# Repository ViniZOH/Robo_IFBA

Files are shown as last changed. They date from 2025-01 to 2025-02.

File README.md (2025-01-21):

# Principais Modificações

## 21/01/2025 -- Aplicadas no ultimo codigo

-------------------------------------------------------
Principais Problemas
-------------------------------------------------------

1- Desativação do motor fora do range de segurança: Quando o input_mot está fora dos limites de segurança, os motores são desligados, mas o setpoint do PID não é atualizado ou monitorado ativamente.
2- Inconsistência na direção do controle: O controle parece atuar apenas em um sentido (subindo até o setpoint), mas não reativa para corrigir valores que excedam o setpoint.
3- Falta de condições dinâmicas no PID: O PID precisa calcular continuamente e ajustar o motor, independentemente do valor atual de input_mot.
-------------------------------------------------------
Sugestões de Correções
-------------------------------------------------------
1. Atualizar o cálculo do PID continuamente:
O PID deve ser acionado mesmo quando input_mot está fora do intervalo de segurança, garantindo que o sistema tente corrigir para o setpoint.
2. Adicionar lógica para ativar o motor corretamente:
A direção do motor deve ser determinada pela diferença entre input_mot (valor lido no  potenciometro) e set_point_mot (valor alvo do PID).
Lógica Sugerida:
1- Se input_mot < set_point_mot, o motor deve girar em uma direção (para aproximar-se do alvo).
2- Se input_mot > set_point_mot, o motor deve girar na direção oposta (para aproximar-se do alvo).
3- Se input_mot estiver próximo o suficiente do set_point_mot (dentro de uma margem de tolerância), o motor deve parar.

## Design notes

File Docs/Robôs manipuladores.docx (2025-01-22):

“SULLA, que sentava inerte durante o ditato, agora digita rapidamento por alguns segundos e para, removendo completamente a carta.” R.O.R., Karel Capek.

Resumo

Este trabalho relata a recuperação de um equipamento que ficou abandonado no instituto federal da bahia por mais de 10 anos, sem nunca ter sido usado. Um braço robótico RD5NT, da Didactica Itália. A estrutura eletrônica não existia e a estrutura mecânica encontra-se com muitos pontos de oxidação. Ao final do trabalho, o robô foi entregue com nova estrutura de controle de potência, posicionamento dos motores, e uma adaptação técnica para o fechamento do efetuador. As estruturas novas foram montadas com componentes adquiridos pelos alunos. Além disso, o robô passou a ter nova estrutura de programação, mais moderna e flexível. Na introdução será mostrado o robô em questão e discutidos os temas introdutórios da robótica de manipulação. Na etapa de Planejamento serão mostrados os componentes escolhidos e os circuitos montados. Na etapa de Execução será mostrada a programação realizada, os circuitos montados e o estado final do braço robótico. Esse trabalho termina com uma lista de próximos passos para continuar melhorando o equipamento.

Abstract

This work reports the recovery of an equipment left in abandonment in Federal Institute of Bahia for more than 10 years, which was never used. A Robotic Arm RD5NT from Didactica Itália. The electronic strutucture does not exist and the mechanical struture is damaged by oxidation. At the end, the arm was returned with new power and positioning structure, and a technical adaptation for the end effector. The new structures were mounted with componentes acquired by the students. Also, the robot has now a new programming structure, modern and more flexibel. Introduction will be shown the robot in question and discussed the introductory topics of robotics manipulation. In the Planning phase will be shown the chosen components and circuits planned. Execution will shown the control programmed, the assembled circuits and the final state of the robotic arm. This work finishes with possible steps to further improve the equipment.

Introdução

Foi numa peça de teatro chamada Rossum’s Universal Robot, de 1921, do checo Karel Capek, que o termo Robot foi introduzido ao mundo. A palavra tem origem em Robota, que significa trabalho forçado. A peça relata um pedaço da vida de Rossum, um cientista de responsável pela criação de um composto químico cuja aplicação seria na construção de humanoides, com o objetivo de transferir todo o trabalho pesado para eles. Hoje, os robôs que conhecemos fazem trabalhos diversos, desde a complexa manipulação de objetos pesados até as mais tediosas e enfadonhas tarefas de casa.

O que se percebe é o aumento do seu uso, já que as pessoas têm menos tempo disponível para as atividades enfadonhas e repetitivas, e não querem correr riscos com atividades como a troca de peças pesadas num forno a 1200ºC, comuns em ambientes industriais, que têm ganhado competitividade com a aplicação desta tecnologia. Aliás, é nesses ambientes que as maiores vantagens destes sistemas aparecem: menores custos de trabalho, maior precisão e maior produtividade, flexibilidade moderada porém alcançável, graças às reprogramações.

Uma definição atual traria o robô como sistema ou grupo de sistemas mecatrônicos capazes de realizar trabalhos de maneira autônoma ou pré-programada. Como elemento principal desta definição temos a programabilidade. O robô como conhecemos advém do pós desenvolvimento da teleoperação (aplicada até em exploração espacial) e do CNC (controle numérico computadorizado), e logo após começaram as aplicações em que não seria possível a utilização de um homem, como a exploração submarina de longa duração, a exploração exoplanetária, o desarmamento de dispositivos explosivos e a busca em ambientes radioativos. Assim, reforça-se que as aplicações dos robôs não estão reduzindo postos de trabalho, pela substituição de um humano com a sua introdução, e sim aumentando a nossa longevidade.

O robô que foi restaurado neste trabalho é um RD5NT, da Didactica Itália. O exemplar da instituição encontrava-se sem estrutura de programação, sem estrutura eletrônica e com marcas de oxidação, apenas com o funcionamento dos servomotores das juntas e do motor do efetuador preservados, o que motivou a restauração.

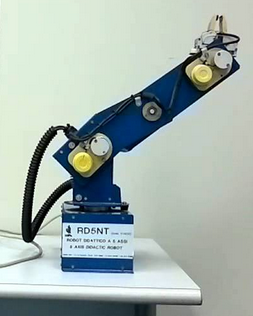
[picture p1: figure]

Trata-se de um braço mecatrônico com 4 servomecanismos de rotação (base, ombro, cotovelo e pulso), 5 elos mecânicos e uma garra mecatrônica. Os elos são as estruturas mecânicas que se ligam entre as juntas, com função de principal de suportar a carga mecânica suportada pelo robô. As juntas que são as estruturas responsáveis pela movimentação e posicionamento e ligam dois elos ou um elo e um efetuador e podem ser do tipo rotacional ou translacional (são os servomecanismos de rotação). Já o efetuador é o dispositivo responsável por realizar a ação proposta, seja ela a soldagem de dois componentes, o suporte de uma peça, a execução de um furo ou o disparo de uma arma. Eles podem ser pneumáticos, mecatrônicos, hidráulicos ou eletromagnéticos.

Além dos componentes citados, um robô precisa para o seu funcionamento de uma unidade de potência para o acionamento correto dos servomecanismos, e uma unidade de controle que proporcionará trajetórias condizentes com a ação a ser efetuada por ele. Para tarefas como complexas como a usinagem de peças para a indústria aeronáutica, por exemplo, o efetuador deve seguir uma trajetória planejada com altíssima precisão. No entanto, para alcançar a melhor estratégia de controle é necessário um modelo matemático do robô. Tal modelagem não foi alcançada, por restrições de tempo do projeto. Além da unidade de controle, é necessária também uma unidade de processamento, responsável por informar a unidade de controle qual posição deve ser alcançada pelo sistema, muitas vezes com restrições de tempo e velocidades bem severas. Esta unidade lê as posições (indicadas provavelmente, por um homem), planeja a movimentação, e se comunica com o espaço exterior, quando necessário.

Para as unidades de controle e processamento, foi adquirido um sistema Arduíno e para as unidades de potência foram adquiridos circuitos do tipo Ponte H (L298N). As características básicas dos componentes adquiridos serão detalhadas na parte de planejamento.

Os robôs manipuladores podem ser classificados por vários critérios, tais como sua geometria, ou estrutura cinemática, o tipo de aplicação para a qual foram projetados, a maneira pela qual são controlados, etc. O robô em questão possui as juntas de rotação numa configuração esférica, seguida por mais dois graus de liberdade de rotação e o efetuador final. A esse tipo é dado o nome RRR (como 3 rotações em sequência). Tem arranjo cinemático antropomórfico do tipo braço.

Planejamento

Levantado o estado atual do robô, no qual verificamos a integridade das conexões entre a porta de saída e os motores, potenciômetros de posição e chave de fim de curso, iniciamos o detalhamento do que seria necessário construir ou comprar para colocar o equipamento em funcionamento. A porta de saída tem vinte e cinco pinos dos quais oito não apresentavam conexão com o robô. As conexões identificadas foram: motor_1, pinos 1 e 14; motor_2, pinos 2 e 15; motor_3, pinos 4 e 17; motor_4, pinos 5 e 18; motor_garra, pinos 6 e 19; Pot_1, pino 20; Pot_2, pino 22; Pot_3, pino 23; Pot_4, pino 24. Os Pinos Vcc e Terra são 13 e 25 respectivamente. O pino 7 está aterrado à carcaça. Os pinos não mencionados estão sem conexão. A figura abaixo mostra a configuração da porta do robô.

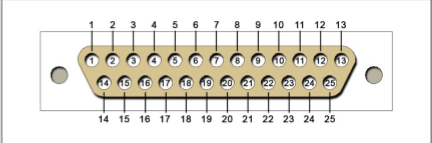
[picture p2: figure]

Como o servomecanismo das juntas é acionadas por motores de corrente contínua, seria necessária a construção de um circuito do tipo Ponte H, para fazê-lo movimentar-se em ambas as direções. Foi adquirida a ponte L298N, uma ponte H completa, com alimentação em 5V e pino de ativação e desativação, capaz de suprir dois motores dc com 2A ou um motor dc com 3A, ou um motor de passo. Na figura abaixo verificamos o desenho esquemático do componente.

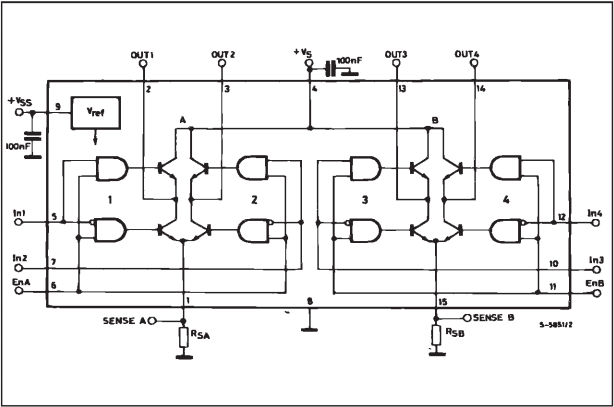
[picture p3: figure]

A ponte integra duas saídas de potência. As duas saídas estão em configuração ponte. Cada ponte é conduzida através de dois gates na entrada e um pino de ativação e desativação. Quando este não tem tensão de alimentação a ponte está no modo desativada. Cada fonte deve ser ligada ao sinal de saída por um caminho bem curto. Para um controle bidirecional de um motor DC é necessário apenas uma das saídas, ou seja, é possível controlar dois motores com um componente. Além disso, foi necessário uma ponte externa de diodos, pois a carga indutiva do motor estava dificultando a própria movimentação.

Para fazer o controle de posição do servomecanismo, foi utilizando um Arduíno MEGA, uma placa de microcontrolador baseado no ATmega1280. Ele tem 54 pinos digitais de entrada/saída (dos quais 14 podem ser usados como saídas PWM), 16 entradas analógicas, 4 UARTs (portas seriais de hardware), um cristal oscilador de 16 MHz, uma conexão USB, um entrada para alimentação e um botão de reset. Ele contém tudo o necessário para apoiar o microcontrolador; basta conectá-lo a um computador com um cabo USB ou ligá-lo com um adaptador AC para DC ou bateria.

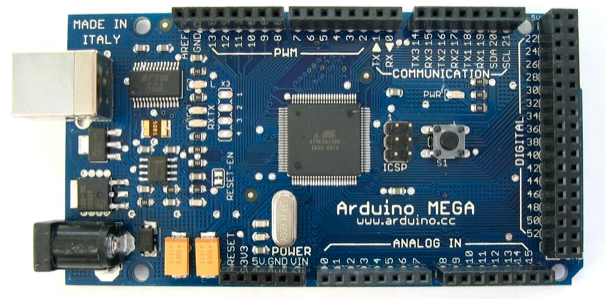
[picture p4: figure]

Com o Arduíno foi possível ler os sinais de tensão dos potenciômetros das juntas, e acionar os circuitos de das entradas das pontes com PWM. Com a saída PWM foi possível controlar com precisão a quantidade de tensão que aciona cada motor e assim realizar o controle de posição e de fechamento da garra.

Além do material descrito, foi utilizada uma fonte de tensão variável para a alimentação dos motores, garra e circuito eletrônico.

Execução

Para a execução do projeto, primeiro foi soldada uma conexão que facilita-se o acesso a porta do robô. Após, realizou-se a verificação das pontes e testou-se o acionamento dos motores direto por elas, verificando a necessidade de 3 pontes para o acionamento de todos os motores do braço antropomórfico.

Foram verificados os limites de movimentação de cada motor e associados a tensão associada fornecida por cada potenciômetro, de modo que para a posição inferior de cada junta haveria um limite de tensão inferior e para cada última posição um limite superior de tensão, sendo possível realizar uma interpolação linear entre os valores. Este mesmo mapeamento foi traduzido numa escala digital para comparação direta com o nível de tensão produzido pelo PWM do Arduíno.

As pontes foram conectadas ao Arduíno, com os pinos de entrada ligados aos pinos de PWM e os pinos de ativação ligados às saídas lógicas do microcontrolador. Após a primeira automação com mudança de direção de movimentação, verificou-se que seria necessária uma ponte de diodos para bloquear a energia acumulada nas bobinas do motor e permitir uma mudança de direção mais rápida. A foto abaixo mostra o estado final do protótipo funcional.

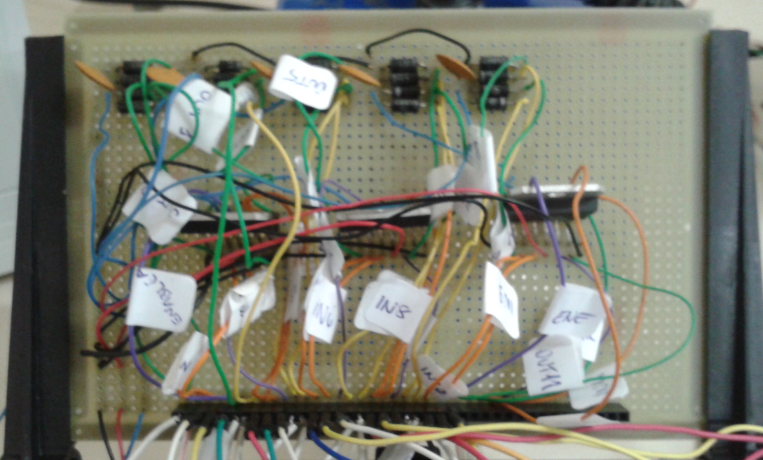
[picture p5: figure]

A partir deste ponto o trabalho tornou-se basicamente de programação. Dentro da unidade Arduíno foi construído um programa que realiza o controle de posição das juntas. Determinamos a posição desejada e aplicamos tensão nos motores até que a posição alcançada esteja de acordo com o solicitado. A posição atual é medida pelo nível de tensão do potenciômetro que é comparada com o nível equivalente à posição de referência. Depois disso o motor é acionado para modificar a sua posição girando para o lado necessário. A posição da junta é novamente calculada e o processo se repete até que a posição solicitada seja alcançada. O diagrama de blocos abaixo retrata o algoritmo utilizado.

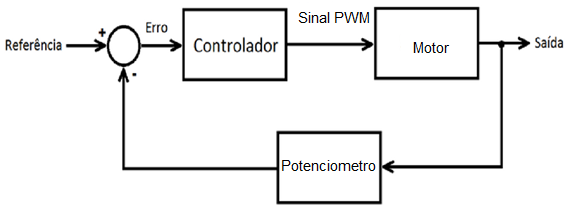
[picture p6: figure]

O algoritmo de controle implementado foi do tipo PID, para o qual apenas a parte proporcional foi utilizada. A estrutura básica de cálculo é reproduzida abaixo. A estrutura na íntegra pode ser visualizada no anexo 1.

error = Setpoint[l] - Input[l];

errSum[l] += (error * timeChange);

dErr = (error - lastErr[l])/timeChange;

Output[l] = (k[l][0])*error + (k[l][1])*errSum[l] + (k[l][2])*dErr;

As etapas do algoritmo descrito acima realizam os seguintes procedimentos:

- calcule a diferença entre posição desejada e posição atual do loop

- calcule o erro acumulado na execução de um loop

- calcule o diferencial do erro em um loop

- calcule e aplique a tensão de saída do loop com base nos parâmetros acima.

Com isso conseguiu-se restaurar a função básica do manipulador, que seria a função de posicionamento. O algoritmo foi implementado para cada uma das juntas rotativas, obtendo sucesso no posicionamento da estrutura em todas elas.

Além do mostrado, foi introduzida uma adaptação técnica à garra, com fins de indicar o fechamento da mesma. A garra só possuía indicador de abertura máxima, realizada por uma chave de fim de curso. A adaptação constiui-se de um circuito de toque, normalmente aberto.

Próximos passos

Há dois pontos cruciais que não foram visitados durante a execução deste projeto. O primeiro é a modelagem da estrutura dinâmica do robô, incluindo as juntas e os elos. Sem essa modelagem não é possível realizar a sintonização da estrutura PID desenvolvida. Sem uma estrutura de PID sintonizada não é possível obter a melhor dinâmica do robô, e deslocamentos em tempos mínimos, além de que, a máxima precisão de posicionamento não é se torna alcançável. É possível o desengripamento das juntas de rotação e substituição das molas de contrabalanceamento.

O segundo ponto crucial é o de determinação da geometria do robô. Sem isso o espaço de trabalho do mesmo é desconhecido, não sendo possível entender em qual zona deste há maior agilidade para a movimentação e reposicionamento de objetos.

Outras ações para o melhoramento futuro da programação são: desenvolvimento da comunicação do Arduíno com o Matlab, aumentando o acesso a ferramentas de identificação e controle para o sistema; Desenvolvimento de uma estrutura de cinemática inversa, para determinação automatizada das posições das juntas para uma dada posição de ação no espaço de trabalho; Desenvolvimento de um código para seguimento de instruções de programação de trajetória em modo manual, a qual tem se tornado de uso constante na indústria automotiva, com as funções de soldagem de ponto elétrico.

Construção de uma base com esteiras e sistema de câmera para a implementação de um simulador de movimentação de carga, permitindo o uso contínuo do robô, em várias disciplinas da instituição.

Pode-se realizar a construção de uma placa apropriada para o sistema de potência do robô, deixando-o independente de fonte externa, com alimentação própria.

Referências

http://www.tech.dmu.ac.uk/~mgongora/Resources/L298N.pdf

http://arduino.cc/en/Main/arduinoBoardMega

ANEXO 1

* Configurando array para medida dos ultimos tempos medidos

*/

unsigned long lastTime[4];

//-------------------------------------------------------------------------------------//

/*

Definindo variavel para controle de inputs e outputs e setpoints

cada linha representa o elo

*/

double Input[4], Output[4], Setpoint[4];

//-------------------------------------------------------------------------------------//

/*

Definido arrays para somatorio dos erros e ultimos erros

*/

double errSum[4]={0,0,0,0},lastErr[4]={0,0,0,0};

//-------------------------------------------------------------------------------------//

/*

configuração do array de ganho dos elos

o numero da linha corresponde o do numero do elo a ser controlado

a coluna corresponde a função de ganho na ordem

1)proporcional

2)integral

3)derivativo

*/

double k[4][3]={{5,0,0},{5,0,0},{5,0,0},{5,0,0}};//arrays com os valores de kp,kd,ki

//----------------------------------------------------------------------------------------//

/*configuração do array de pinos para controle dos elo

linhas representam o elo a ser controlado e colunas as a funcionalidade do tipo

controle do elo 1 (linha 0) o pulso:

pino potenciometro 1 será 1

pino do input 1 do motor 2 será 6

pino do input 2 do motor 2 será 7

pino do enable motor 2 será 33

controle do elo 2 (linha 1)o cotovelo:

pino potenciometro 2 será 2

pino do input 1 do motor 3 será 8

pino do input 2 do motor 3 será 9

pino do enable motor 3 será 35

controle do elo 3 (linha 2)o ombro:

pino potenciometro 3 será 3

pino do input 1 do motor 4 será 10

pino do input 2 do motor 4 será 11

pino do enable motor 4 será 37

controle do elo 4 (linha 3)o ombro:

pino potenciometro 4 será 4

pino do input 1 do motor 5 será 12

pino do input 2 do motor 5 será 13

pino do enable motor 5 será 39

*/

int pino[4][4] = {{1,6,7,33},{2,8,9,35},{3,10,11,37},{4,12,13,39}};

//---------------------------------------------------------------------------------------//

/*configuração de valores medidos

para leitura minima e maxima da entrada analogica

Alimentação do fonte Vs=4.9V

Alimentação da fonte Vss=4.9V

vetor chamado de limites

1)linhas indicam o potenciometro

2)1ª Coluna indica valor maximo de deslocamento angular em relação a referencia

3)2ª Coluna indica valor minimo de setpoint medido pelo arduino

4)3ª COluna indica valor maximo de setpoint medido pelo arduino

*/

double limites[4][3]={{360,0,1023},{293,66,900},{96,376,648},{291,101,928}};

//----------------------------------------------------------------------------------//

unsigned long now;

double timeChange;

double error;

double dErr;

double lasttime;

int condicao;

void setup(){

Serial.end(); //eliminando qualquer configuração serial anterior

//configurando pinos de entrada

for(int i = 0;i<4;i++){

pinMode(pino[i][0],INPUT);

//configurando pinos de saída

for (int j=1;j<4;j++){

pinMode(pino[i][j],OUTPUT);

}

}

pinMode(41,OUTPUT); //Enable do motor 1 - garra

pinMode(43,OUTPUT); //Input 2 do motor 1

pinMode(45,OUTPUT); //Input 1 do motor 1

Serial.begin(57600); //configurando entrada serial

//Verificar estado inicial que se quer da garra

condicaogarra();

//Impondo a codição angular desejada usando a funcao converte angulo detalhes abaixo

for(int i=0;i<4;i++){

Setpoint[i] = converteangulo(i);

}

//iniciando os valores do tempo dos lastTime medidos

for(int j=0;j<4;j++){

lastTime[j]=millis();

}

}

//----------------------------------------------------------------------------------//

void loop()

{

//laço para leitura de todos os potenciometros

Input[0] = analogRead(A1); //potenciometro 1

Input[1] = analogRead(A2); //potenciometro 2

Input[2] = analogRead(A3); //potenciometro 3

Input[3] = analogRead(A4); //potenciometro 4

Serial.println();Serial.println("Diferenca de setpoint");

Serial.print(Setpoint[0]-Input[0]);Serial.print(" | ");

Serial.print(Setpoint[1]-Input[1]);Serial.print(" | ");Serial.print(Setpoint[2]-Input[2]);

Serial.print(" | ");Serial.print(Setpoint[3]-Input[3]);Serial.println(" | ");Serial.println();

//

for(int l=0;l<4;l++){

now = millis();

timeChange = (double)(now - lastTime[l]);

error = Setpoint[l] - Input[l];

errSum[l] += (error * timeChange);

dErr = (error - lastErr[l])/timeChange;

Output[l] = (k[l][0])*error + (k[l][1])*errSum[l] + (k[l][2])*dErr;

//Output[elo] = abs(Output[elo]);

lastErr[l] = error;

lastTime[l] = now;

if(Output[l]>0){

Output[l]=abs(Output[l]);

Output[l]=constrain(Output[l],0,1023);

Output[l]=map(Output[l],0,1023,0,255);

analogWrite(pino[l][1], 0); //acionando input 1 desde que condição de sentido favoravel

analogWrite(pino[l][2], Output[l]); //acionando input 2 desde que condição de sentido favoravel

digitalWrite(pino[l][3],HIGH); //habilitando enable

}

else{

Output[l]=abs(Output[l]);

Output[l]=constrain(Output[l],0,1023);

Output[l]=map(Output[l],0,1023,0,255);

analogWrite(pino[l][1], Output[l]); //acionando input 1 desde que condição de sentido favoravel

analogWrite(pino[l][2], 0); //acionando input 2 desde que condição de sentido favoravel

digitalWrite(pino[l][3],HIGH); //habilitando enable

}

}

Serial.println();Serial.println("Valores do PID");

Serial.print(Output[0]);Serial.print(" | ");

Serial.print(Output[1]);Serial.print(" | ");Serial.print(Output[2]);

Serial.print(" | ");Serial.print(Output[3]);Serial.println(" | ");

Serial.println();

if (Serial.available())

{

//Impondo a codição angular desejada usando a funcao converte angulo detalhes abaixo

for(int i=0;i<4;i++)

{

Setpoint[i] = converteangulo(i);

}

}

}

//----------------------------------------------------------------------------------//

/*

Funcao que fornece o deslocamento angular desejado

*/

double converteangulo(int elo){

Serial.print("Digite o deslocamento para ");

switch(elo){

case 0:

Serial.print("o Pulso 0-");

break;

case 1:

Serial.print("o Cotovelo 0-");

break;

case 2:

Serial.print("o Ombro 0-");

break;

case 3:

Serial.print("a Base 0-");

break;

}

Serial.print(limites[elo][0]);Serial.println(" em graus:");

while(!Serial.available());

double x =Serial.parseInt();

double deslocamento = map(x,0,limites[elo][0],limites[elo][1],limites[elo][2]);

return(deslocamento);

}

void condicaogarra(){

Serial.print("Deseja-se garra aberta( digite 1) ou fechada(digite 2): ");

while(!Serial.available());

condicao=Serial.parseInt();

if(condicao==1){

abrirgarra();

}

else{

fechargarra();

}

Serial.println();

}

void abrirgarra(){

digitalWrite(41,HIGH);//Enable do motor 1

digitalWrite(43,HIGH);//Input1 do motor 1 alto

digitalWrite(45,LOW);//Input2 do motor 2 baixo

}

void fechargarra(){

digitalWrite(41,HIGH);//Enable do motor 1

digitalWrite(43,LOW);//Input1 do motor 1 baixo

digitalWrite(45,HIGH);//Input2 do motor 2 alto

}

//----------------------------------------------------------------------------------//

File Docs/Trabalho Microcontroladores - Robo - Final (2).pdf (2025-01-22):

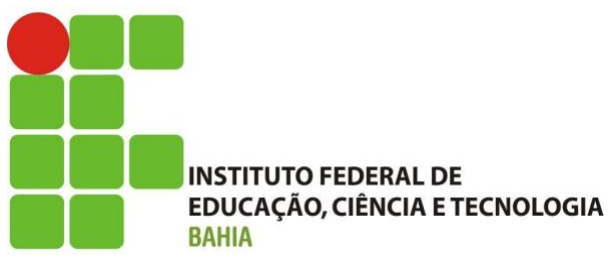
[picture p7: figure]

DEPARTAMENTO DE TECNOLOGIA EM ELETRO-ELETRÔNICA

COORDENAÇÃO DE ENGENHARIA INDUSTRIAL ELÉTRICA

LEANDRO DINIZ FERREIRA

CONTROLE PID APLICADO A UM ROBÔ MANIPULADOR ELETROMECÂNICO

COM O AUXÍLIO DO MICROCONTROLADOR ARDUINO

SALVADOR, BA

SETEMBRO DE 2014

LEANDRO DINIZ FERREIRA

CONTROLE PID APLICADO A UM ROBÔ MANIPULADOR ELETROMECÂNICO

COM O AUXÍLIO DO MICROCONTROLADOR ARDUINO

SALVADOR, BA

SETEMBRO DE 2014

Trabalho apresentado ao professor

Eduardo | Telmo | da | disciplina

microprocessamento e microcontrole

como requisito parcial para obtenção

da média semestral.

SUMÁRIO

### 1 INTRODUÇÃO

A aplicação de robôs na indústria evidencia numerosos benefícios, dos quais

pode-se enumerar o aumento da produtividade, consistência e melhoria da qualidade do

produto final, confiabilidade do processo, facilidade de programação e substituição da

atividade de determinados robôs, operação em ambientes insalubres e de alta

periculosidade, entre outros.

Dessa forma, a implementação de braços robóticos para execução de determinadas

tarefas como pintura, soldagem, movimentação de cargas, inspeção de produtos e

montagem é sinônimo de agilidade e precisão com segurança na indústria, sem expor a

vida humana.

Em contrapartida, além dos ambientes hostis, a utilização de braços robóticos

somente na linha de produção tem contrastado com aplicação em locais antes não imaginados. É o caso da companhia C & S Wholesale Grocers, a maior distribuidora de

produtos alimentícios dos Estados Unidos, que está empregando robôs para carregar,

organizar e armazenar seus estoques de forma mais eficiente do que a mão de obra

humana[5].

O processo de automação industrial também tem levantado muitas discussões a

respeito do desemprego de trabalhadores. No entanto, especialistas defendem que a

aplicação de novas tecnologias apenas substitui a qualificação profissional, gerando

empregos em outras áreas. De fato, a presença do trabalho humano é extremamente

importante no processo de inovação e questionamento a respeito do processo produtivo,

bem como na programação dos robôs. Sendo assim, a familiarização dos profissionais da

área com os braços eletromecânicos deve fazer parte da sua qualificação.

### 1.1 OBJETIVOS

### 1.1.1 Objetivo Geral

O objetivo geral deste estudo é implementar um circuito capaz de acionar e

controlar um braço robótico didático, o RD5NT fabricado pela Didacta Itália, colocando-

o numa posição desejada.

### 1.1.1 Objetivos Específicos e Metodologia

I. Esquematizar e montar um circuito amplificador utilizando o circuito integrado

L298N.

II. Utilizar o Arduino Mega como placa controladora para efetuar os ensaios de

coleta dos valores do potenciômetro e em seguida convertê-los em graus.

III. | Implementar e gravar no microcontrolador do Arduino | Mega, ATmega1280, um

programa que seja capaz de controlar o posicionamento do braço robótico através

| da estratégia de controle PID.

### 2 ESTRUTURA DO RD5NT

O robô RD5NT é um braço eletromecânico composto de cinco graus de liberdade

fabricado pela empresa Didacta Itália. Trata-se de um robô com quatro eixos de rotação

e uma garra, sendo que cada eixo e a garra possuem um motor DC e um potenciômetro

rotativo linear que funciona como um encoder.

Os motores DC possuem velocidade de rotação alta sendo necessária relação de

engrenagens capazes de reduzir a velocidade do eixo. Sendo assim, a transmissão de cada

movimento é feita através de um bloco redutor que inclui o motor DC e as engrenagens.

Os potenciômetros acompanham o movimento do eixo e da garra, modificando

sua resistência de forma linear. O aspecto linear assegura o posicionamento angular de

cada eixo, possibilitando um mapeamento da queda de tensão sobre a resistência daquela

posição angular. Por exemplo, o pulso representado na Figura 1 possui liberdade de

rotação que vai de 0º a aproximadamente 360º. Como o valor do potenciômetro é ajustável

de 0 a 5kΩ, é possível estabelecer uma relação linear entre a posição angular e o valor da

resistência lida:

θ =

360
5000 Rf

(1)

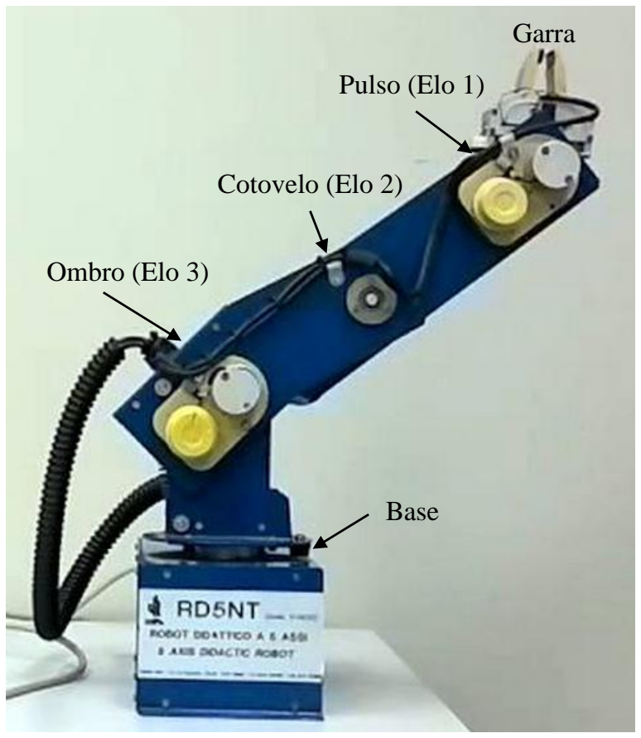
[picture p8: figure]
Pulso (Elo 1); Cotovelo (Elo 2); Ombro (Elo 3); Base; Garra

Figura 1 - Robô RD5NT

A tabela relaciona os arcos em graus de rotação de cada elo. Os valores da

resistência foram lidos com o auxílio do Arduino em valores binários e posteriormente

convertidos em graus utilizando através da Eq. (1).

Tabela 1 – Arcos permissíveis de cada eixo
Eixo | Arcos de rotação
Pulso | 0 a 360º
Cotovelo | 0 a 293º
Ombro | 0 a 96º
Base | 0 a 291º

A Figura 2 mostra o conector DB fêmea de 25 pinos, que fica localizado na base fixa do robô manipulador. É através desse conector que ocorre a troca de dados entre o

robô manipulador e o microcontrolador do Arduino Mega. A Tabela 2 relaciona os pinos

para alimentação dos motores de corrente contínua e os que recebem os sinais de saída

do potenciômetro e também a alimentação dos potenciômetros (5V).

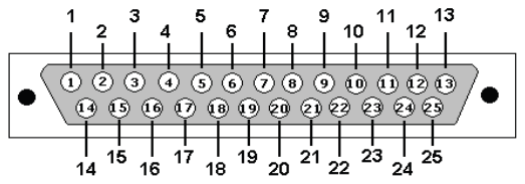
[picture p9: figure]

Figura 2 – Relação de pinos do RD5NT

Tabela 3 - Pinagem do RD5NT
Pinos | Função | Pinos | Função
1 | Motor 1 | 14 | Motor 1
2 | Motor 2 | 15 | Motor 2
3 | Chave de fim-de-curso | 16 | Não utilizado
4 | Motor 3 | 17 | Motor 3
5 | Motor 4 | 18 | Motor 4
6 | Motor 5 | 19 | Motor 5
7 | Não utilizado | 20 | Potenciômetro 4
8 | Não utilizado | 21 | Potenciômetro 3
9 | Não utilizado | 22 | Potenciômetro 4
10 | Não utilizado | 23 | Não utilizado
11 | Não utilizado | 24 | Potenciômetro 1
12 | Não utilizado | 25 | Energização potenciômetro
13 | Energização potenciômetro

### 3 ESTRATÉGIA DE CONTROLE PID

Tendo como objetivo geral do projeto o controle de posicionamento dos eixos,

escolheu-se a estratégia de controle proporcional-integral-derivativo (PID) devido a sua

difusão nesse tipo de objetivo.

O PID é um mecanismo de controle de malha fechada amplamente utilizada em

sistemas industriais. Basicamente, um controlador PID efetua a subtração entre uma

variável de processo medida e um ponto de ajuste desejado.

O algoritmo de controle PID envolve três parâmetros: o proporcional, os valores

integrais e derivados. Simplificando, estes valores podem ser interpretados em termos de

tempo: P depende do erro presente, I sobre a acumulação de erros no passado, e D é uma

previsão de futuros erros, com base na taxa atual de mudança. A soma ponderada destas

três ações é usada para ajustar o processo por meio de um elemento controlado, tal como

a posição de uma válvula de controle, um amortecedor, ou a potência fornecida a um

elemento de aquecimento[4].

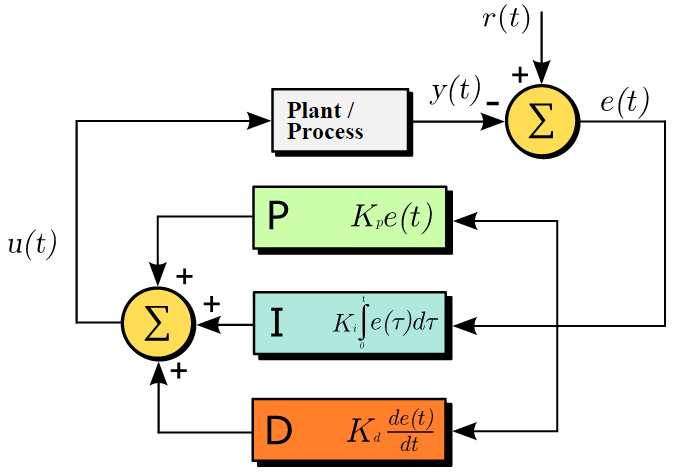
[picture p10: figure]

Figura 3- Malha de controle PID
Na ausência de conhecimento do modelo matemático do processo, o controlador

PID tem sido aplicado com mais frequência. Ao ajustar os três parâmetros do algoritmo

controlador PID, o controlador pode proporcionar uma ação de controle concebido para

as necessidades específicas do processo. A resposta do controlador pode ser descrita em

termos de capacidade de resposta do controlador a um erro, o grau em que o controlador

ultrapassa o valor de ajuste, e o grau de oscilação do sistema. Nota-se que o uso do

algoritmo PID para controle não garante um controle otimizado do sistema ou sistema de

estabilidade.

### 4 COMPONENTES DO CIRCUITO

O diagrama de blocos e componentes do circuito é mostrado na Figura 4. A escrita

e gravação do programa no microcontrolador é efetuada com o auxílio no notebook. O

microcontrolador lê o posicionamento de cada eixo rotativo e executa o programa. Em

seguida, envia para as saídas PWM valores de tensão que serão amplificados no circuito

amplificador com L298 para então acionar os motores cc. A posição angular é modificada

com o acionamento do motor cc e sua nova posição é lida no próximo ciclo do

microcontrolador.

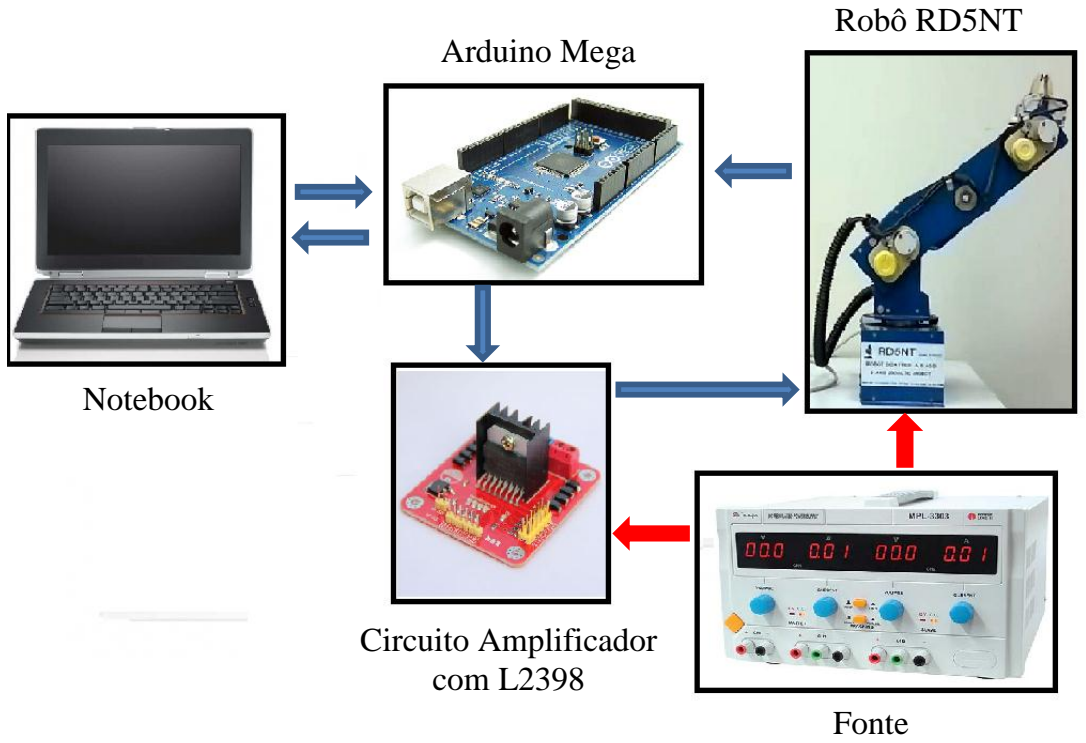
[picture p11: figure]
Notebook; Arduino Mega; Circuito Amplificador com L2398; Fonte; Robô RD5NT

Figura 4- Diagrama de blocos e componentes do circuito

### 4.1 O MICROCONTROLADOR – ARDUINO MEGA

O circuito de acionamento dos motores necessita de um microcontrolador para

efetuar a leitura do posicionamento angular de cada eixo, comparar com a posição

desejada (Setpoint) e efetuar o controle PID. Sendo assim, devido a praticidade,

utilizaremos o Arduino Mega como elemento de processamento do circuito.

O Arduino Mega é uma placa de microcontrolador baseado no ATmega1280. Ele

possui 54 pinos digitais de entrada / saída (dos quais 14 podem ser usados como saídas

PWM), 16 entradas analógicas, 4 UARTs (portas seriais de hardware), um cristal

oscilador de 16 MHz, uma conexão USB, um jack de alimentação, protocolo de

comunicação ICSP, e um botão de reset. Ele contém tudo que é necessário para apoiar o

microcontrolador, basta conectá-lo a um computador com um cabo USB ou ligá-lo com

um adaptador AC para DC ou bateria para começar. O Mega é compatível com a maioria

dos shields projetados para o Arduino Duemilanove ou Diecimila.

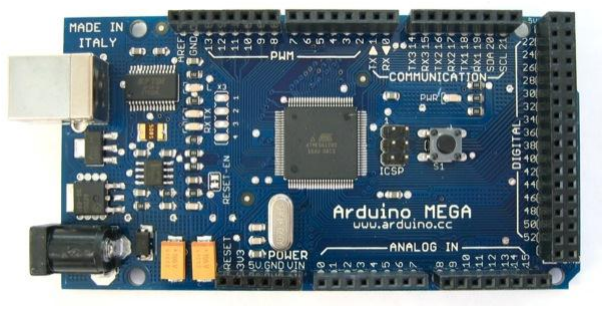
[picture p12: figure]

Figura 5 - Arduino Mega

Fonte: Imagem disponível em: <http://arduino.cc/en/Main/arduinoBoardMega>. Acesso em 14/09/2014
Para o projeto de acionamento do robô RD5NT utilizaremos as saídas PWM para

acionamento dos motores DC por meio de pontes H, as entradas analógicas para leitura

de posição do eixo rotativo através do potenciômetro linear e as saídas digitais para

controle dos enables dos respectivos motores através da ponte H. As saídas PWM serão

usadas para gerar tensões com valores controlados pelo programa.

### 4.2 PONTE H DUPLA L298

O L298 é um circuito integrado de ponte H dupla desenvolvida para aceitar

padrões de nível lógico TTL e acionar cargas indutivas tais como relés, solenoides,

motores DC e motores de passo. Dois “enables” foram desenvolvidos para permitir ou

não permitir o acionamento da carga independentemente uma da outra. O L298 foi

utilizado no projeto para acionar os motores CC presente nos elos do braço do robô

RD5NT.

O diagrama de blocos é mostrado na Figura 6. Os emissores dos transistores mais

inferiores de cada ponte são conectados juntos e no terminal correspondente pode ser

adicionado um resistor externo como um sensor de corrente.

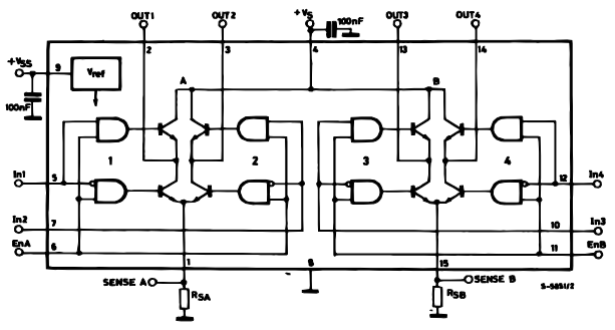
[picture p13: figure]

Figura 6 - Diagrama de blocos do L298

Fonte – Datasheet L298. STMicroelectronics

O CI foi configurado de forma que a alimentação lógica seja independente da

alimentação de força, fazendo com que o circuito lógico trabalhe numa tensão menor.

Existe dois tipos de circuito fabricado pela STMicroelectronics: a Multiwatt15 e a

PowerSO20. Neste projeto utilizou-se a Multiwatt15 mostrada na Figura 7.

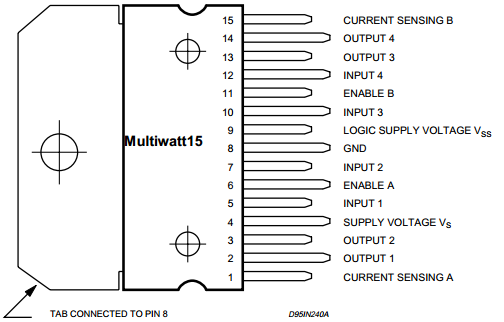
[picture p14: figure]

Figura 7- Configuração Multiwatt15 utilizado no projeto do robô

Fonte – Datasheet L298. STMicroelectronics

As tensões de operação que são recomendadas pelo fabricante são: tensão de

alimentação 12V e tesão lógica 5V. E são essas tensões que foram utilizadas no projeto.

O método de acionamento de um motor CC bidirecional é mostrado na Figura 8,

juntamente com a combinação de entradas e a direção de rotação do motor. Os diodos efetuam o papel de proteção contra correntes reversas e o capacitor o de tornar a tensão

mais estável.

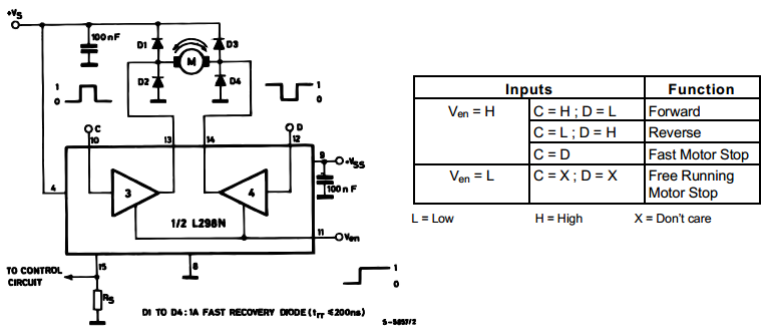
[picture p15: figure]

Figura 8 - Método de acionamento de um motor DC bidirecional

Fonte – Datasheet L298. STMicroelectronics

Cada L298 é capaz de acionar dois motores CC bidirecionalmente, sendo,

portanto, necessário três CI L298 para acionarem cinco motores CC presentes na estrutura

do braço automático RD5NT.

### 4.3 FONTE

No projeto, foi utilizada a fonte de alimentação simétrica DC Digital Minipa.

Trata-se de um equipamento digital de bancada, com quatro displays de 3 dígitos (duas

de tensão e duas de corrente), capaz de fornecer duas saídas variáveis com tensão de 0 a

30V DC e corrente de 0 a 3A DC, e uma saída fixa de 5V / 3A DC. Possui proteção de

sobrecarga e inversão de polaridade, e a duas saídas variáveis podem ser ligadas em série

ou paralelo através do painel frontal.

A fonte foi responsável por alimentar o circuito de força (7-12V) e o circuito

lógico 5V. Já o Arduino foi alimentado através da porta USB.

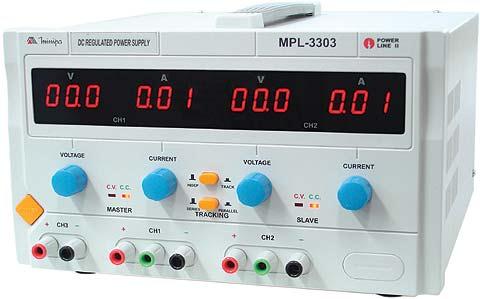
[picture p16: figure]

Figura 9 - Fonte de alimentação utilizada.

Fonte: Imagem e descrição disponível em:< http://www.mreferramentas.com.br/>

### 5 CONTROLE DO POSICIONAMENTO DO PULSO

Inicialmente, estudaremos o controle de posição de somente um motor. O

esquemático da Figura 10 mostra o circuito de acionamento do motor DC do Pulso do

robô manipulador. Os pinos que serão utilizados do Arduino são:

- Entrada analógica: A1
- Saídas PWM de acionamento: 6 e 7
- Saída digital para o enable: 33

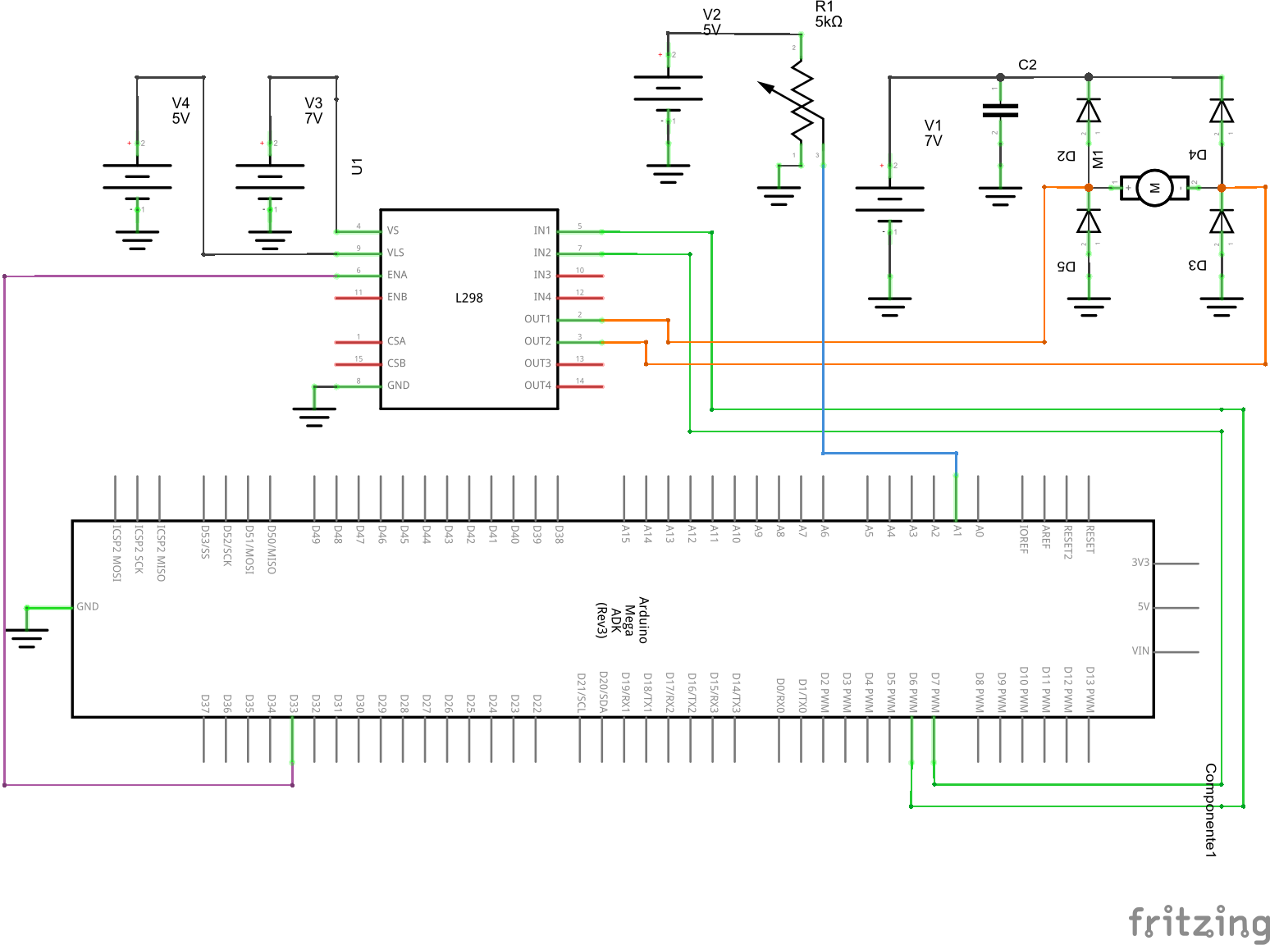
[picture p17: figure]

Figura 10 - Esquemático de acionamento do um motor

Fonte: Circuito montado com o auxílio do software Fritzing

Basicamente o programa deve ler o valor do potenciômetro, transformar esse valor

no seu equivalente em graus e comparar com o valor de posição angular desejado. A

diferença entre esses dois valores deve ser aplicada a um controle PID e a saída deve ser

enviada em valores de tensão em PWM. Esse valor é amplificado e então aplicado ao

motor cc.

Iniciamos a escrita do programa definindo as variáveis que serão utilizadas

conforme mostra a Figura 11. As variáveis Kp, Ki e Kd são as constantes do controle PID

e são ajustadas de acordo com o desempenho do controle.

Figura 11 - Definição das variáveis
Em seguida, inicializaremos o programa e a placa através da função setup

conforme mostra Figura 12. Quando a placa é ligada ou resetada, essa função é executada. É através dela que informa-se ao hardware do Arduino o que será utilizado dele. Dessa

forma, informamos que utilizaremos os pinos 6 e 7 como saídas PWM de acionamento

do motor, o pino 33 como enable e o pino 1 como entrada do sinal medido do

potenciômetro. A Figura 10 mostra as ligações desses pinos.

Ainda nesta etapa, efetua-se um print para comunicação da necessidade de entrada

do valor desejado do posicionamento angular em graus. O valor em graus é armazenado

na variável x através da função Serial.parseInt() e em seguida é transformada em binário

através da função map(x,0,360,1023).

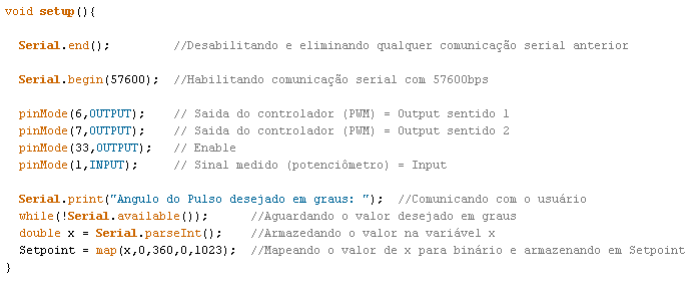
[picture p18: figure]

Figura 12 - Função Setup
A próxima etapa do programa é o loop principal do programa. Esta etapa é

executada indefinidamente até que a placa seja desligada ou resetada. No entanto, como dentro desse loop uma sub-rotina responsável pelo cálculo PID será chamada,

debruçaremos primeiro sobre ela, a função Compute() mostrada na Figura 13.

Quando a sub-rotina Compute() é chamada, ela inicia definindo a variável now

através da função millis(), que retorna o valor em milissegundos desde que a placa

começou a executar o programa atual. Esse valor será a referência para o cálculo da

variação do tempo. Em seguida, define-se a variável timeChange que irá armazenar a

variação do tempo calculada pela diferença entre as variáveis now e lastTime. A diferença

entre o Setpoint e o Input é armazenada na variável error e será usada para o cálculo das

parcelas proporcional, integral e derivativa. A integral é dada pelo produto da variável

error e timeChange mais o somatório das parcelas anteriores e é armazenado em errSum.

A parcela derivativa é calculada pela divisão da diferença entre error e lastErr por

timeChange. Por fim, a soma do produto dessas parcelas por seus respectivos coeficientes

será armazenada em Output e em seguida é tomado seu módulo. Os valores de error e

now são armazenadas em lastErr e lastime, respectivamente, para que no próximo ciclo

sejam tomadas como referência.

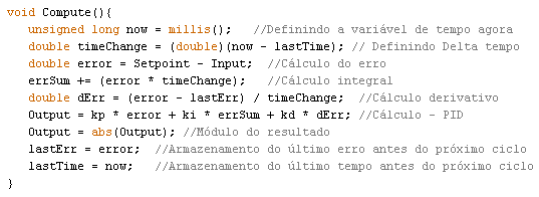
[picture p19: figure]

Figura 13 - Função Compute() onde efetua-se o calculo PID
O loop principal inicia efetuando a leitura do potenciômetro e armazenando esse

valor em Input, vide Figura 14. De posse deste valor, já pode-se efetuar o cálculo PID

através da função compute(), e assim é feito. Após a execução da função compute(), o

resultado do PID já está armazenado na variável Output, bastando efetuar seu tratamento

e enviar para saída do Arduino. A primeira etapa é limitar o valor de Output no intervalo

binário de 0 a 1023. Em seguida, faz-se uma conversão do valor em binário para o

intervalo de 0 a 255 que é o padrão de saída do PWM. O valor 0 possui uma saída de 0V

ao longo do tempo. Já a saída 255 possui o valor de 5V ao longo do tempo. Mas se a saída

for 191, tem-se na saída uma onda quadrada com um duty cicle de 75% em 5V. Por fim,

basta definir qual o sentido de rotação do motor cc. Para isso, basta comparar o valor de

Input que é o valor lido pelo potenciômetro e o Setpoint que é o valor desejado. Se Input

for maior ou igual a Setpoint escreve-se o valor Output padronizado em PWM no pino 7 e o valor nulo no pino 6, seguido da habilitação do enable. Assim, define-se um sentido

de rotação. Caso Input seja menor que Setpoint os valores escritos nos pinos 7 e 6 são

invertidos, seguido da habilitação do enable. Tem-se portanto o sentindo inverso do

anterior.

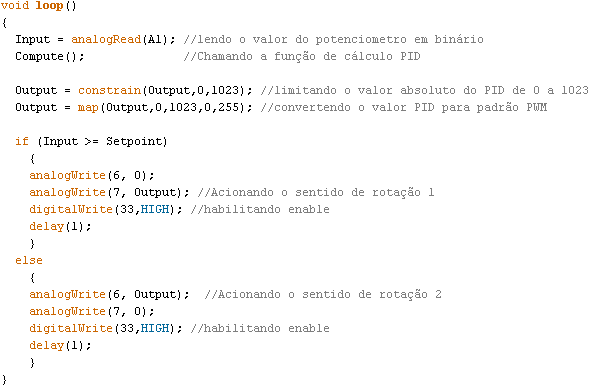
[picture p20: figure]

Figura 14 - Função loop
O programa completo está em anexo a este trabalho. A implementação do

posicionamento dos outros eixos é baseada no programa escrito para o posicionamento

do pulso.

### 6 PROGRAMA DE ACIONAMENTO DO ROBÔ RD5NT

O programa é o Código 2 – Programa de acionamento do RD5NT e encontra-se

no tópico Anexo deste trabalho. Ele pode ser subdividido em 3 etapas: Definição de

variáveis, setup e loop.

A primeira delas é a definição de variáveis. Nesta etapa é definida a maioria das

variáveis que serão utilizadas ao longo do programa. As variáveis Input, Output, Setpoint,

lastTime, errSum são definidas como vetores com quatro posições, referentes a cada

motor. Já as variáveis K, pino e limites (referentes aos limites dos arcos) além de

possuírem as posições referentes a cada motor, devem contemplar as constantes de PID,

os pinos que serão utilizados por cada motor, e os arcos, respectivamente. Sendo assim

são definidas como matrizes. Algumas variáveis de tempo utilizadas no controle PID

serão comuns aos motores, não sendo necessária a distinção pra cada um.

A segunda etapa é o setup. Nela define-se como cada pino será utilizado. A matriz

pino é submetida a uma função for que define os pinos de entrada e saída. Os pinos que

serão utilizados pela garra foram definidos separadamente. Na função setup as funções

condicaogarra() e converteangulo() são executadas de modo a comunicar com o usuário

do programa a necessidade da entrada de dados que são referentes a condição e

posicionamento da garra e dos motores de cada eixo integrante do robô. Nessas funções

são informadas os setpoints desejados e se gostaríamos de fechar ou abrir a garra.

A terceira etapa é a função loop. Aqui os potenciômetros são lidos em valores

binários e diferentemente do programa anterior em que tinha-se uma função dedicada

para o controle PID, essa etapa foi integrada ao loop por conveniência.

### 7 ANÁLISE DOS RESULTADOS E CONCLUSÕES

Os passos da metodologia e dos objetivos do trabalho foram executados com

êxito. Inicialmente foi esquematizado e montado o circuito amplificador com o L298N e

posteriormente testado o funcionamento de cada ponte H integrante do CI, mostrando-se

como resultado o funcionamento conforme previsto no planejamento. Ao aplicar a tensão

em nível lógico, juntamente com o enable habilitado, as pontes H efetuaram o devido

acionamento dos motores cc.

Os ensaios e medições dos valores dos potenciômetros lidos pela placa

microcontroladora também permitiram o devido mapeamento dos arcos disponíveis para

o movimento de cada eixo. Sendo assim, o próximo passo para implementação do

programa que efetuará o controle PID pôde ser executado.

O procedimento de elaboração do programa responsável pelo cálculo PID seguiu

uma lógica simples e de fácil compreensão. Conforme já discutido, o programa iniciou-

se através da definição das variáveis, seguido da execução da função setup, onde

informou-se ao Arduino aquilo que dele seria usado e então efetuou-se a lógica principal

do programa, a função loop. Dentro desta lógica, o cálculo PID é executado a cada ciclo,

ou seja, todo ciclo os potenciômetros são lidos, é efetuado o PID e atualizado o Output.

Em seguida, o resultado obtido e armazenado na variável Output é então escrito na saída

PWM do Arduino. O ajuste dos coeficientes proporcional, integral e derivativo foi obtido

experimentalmente, o que levou a um controle puramente proporcional devido a sua

melhor atuação.

Contudo, o processo evolutivo do acionamento do robô manipulador alcançou os

objetivos que foram estabelecidos no início do trabalho, ou seja, a colocação do robô

numa posição desejada foi alcançada com sucesso.

REFERÊNCIAS BIBLIOGRÁFICA

[1] PINTO, Carlos R. A. Controle adaptativo aplicado em dois elos de um robô eletromecânico de cinco graus de liberdade. 2011. 136 f. Tese (Doutorado em Mecânicaa). Unifersidade Federal da Paraíba, João Pessoa, 2011.
[2] DA COSTA E SILVA, V. e M.; MONTENEGRO, P. H. de M. | Modelamento
em tempo real de três elos de um robô manipulador eletromecânico de cinco graus de liberdade. Asociacón Argentina de Mecânica Computacional, Bueno Aires, v. 29, p. 2229-2241, Nov. 2010.
[3] Motor Control using PWM and PID: Embedded Design. Disponível em: < http://coactionos.com/embedded%20design%20tips/2013/10/15/Tips-Motor-Control-using-PWM-and-PID/ >. Acesso em 10/09/2014.
[4] MITUHIKO, A. Control System, Robotics and Automation: PID Control. Vol-II Kyoto University, Japan.
[5] PID Controller. Disponível em: < http://en.wikipedia.org/wiki/PID_controller >. Acesso em 11/09/2014.
[6] GUILHERME, P. Como os robôs estão mudando o mundo?. Tecmundo Beta, 2012. Disponível em:< http://www.tecmundo.com.br/robotica/28854-como-os-robos-estao-mudando-a-industria-.htm >. Acesso em 11/09/2014.
[7] BASTOS FILHO, T. F. Aplicação de Robôs nas Indústrias. Departamento de Engenharia Elétrica, Universidade Federal do Espírito Santo, 1999.

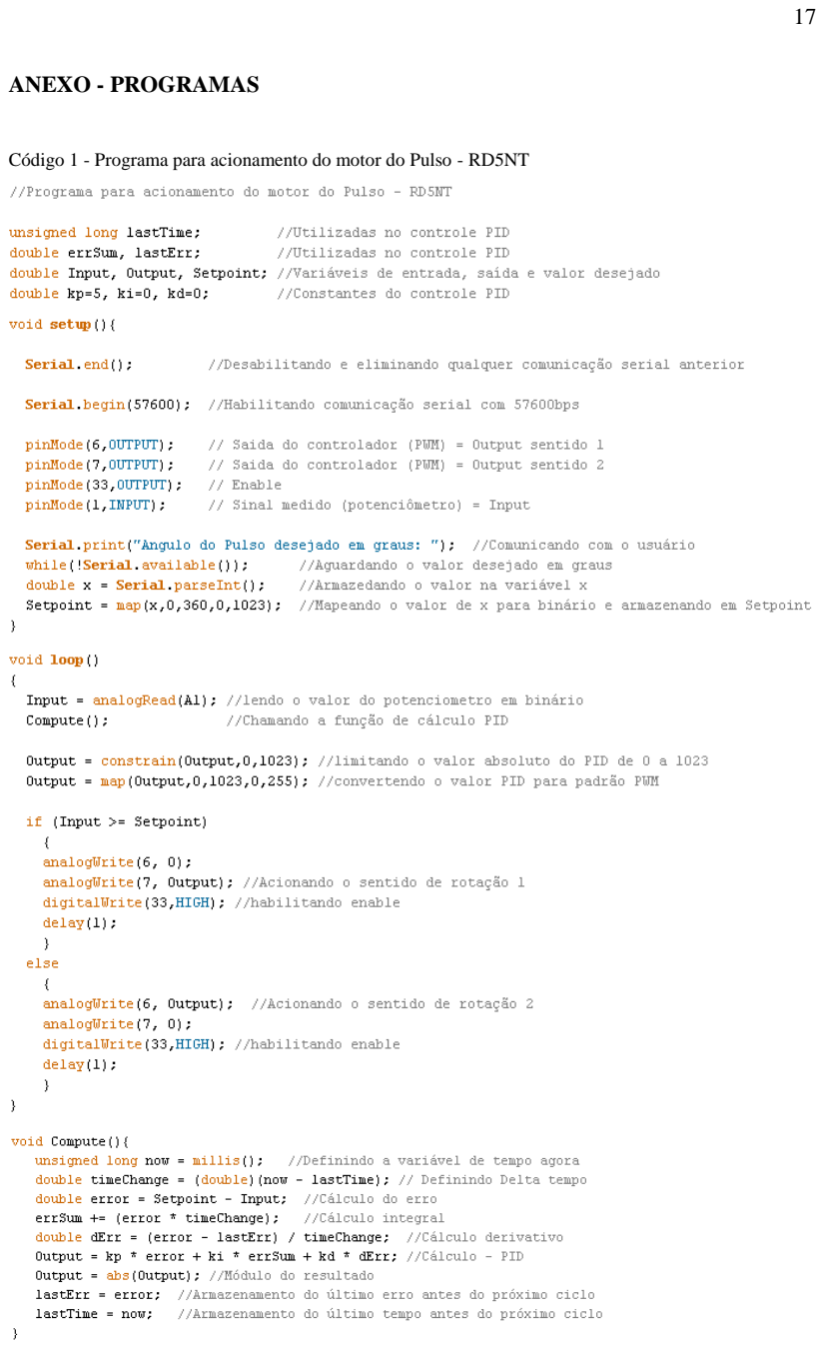
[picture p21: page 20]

ANEXO - PROGRAMAS

Código 1 - Programa para acionamento do motor do Pulso - RD5NT

Código 2 – Programa de acionamento do RD5NT

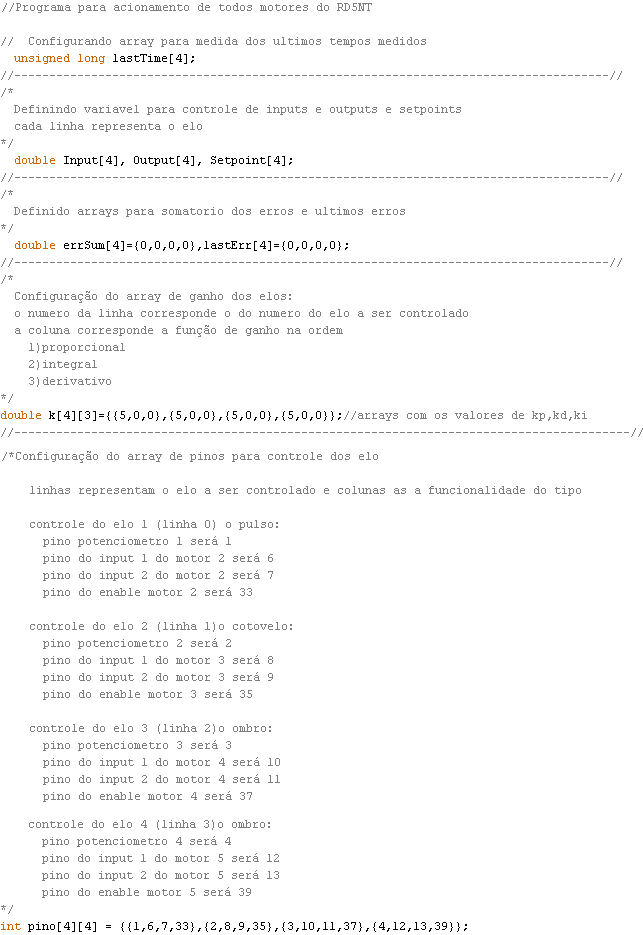
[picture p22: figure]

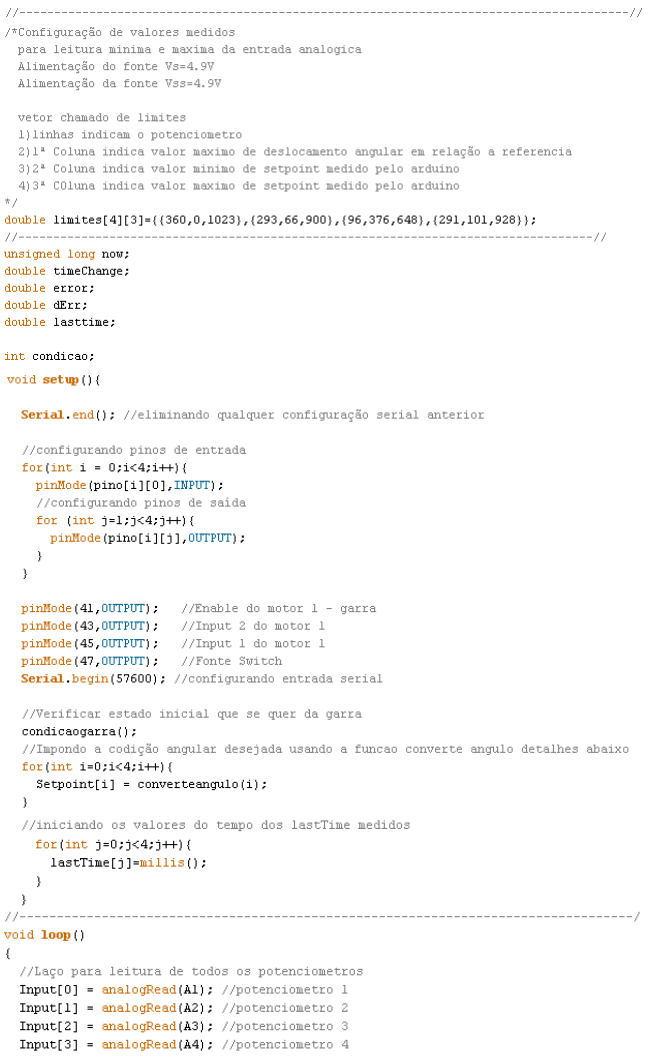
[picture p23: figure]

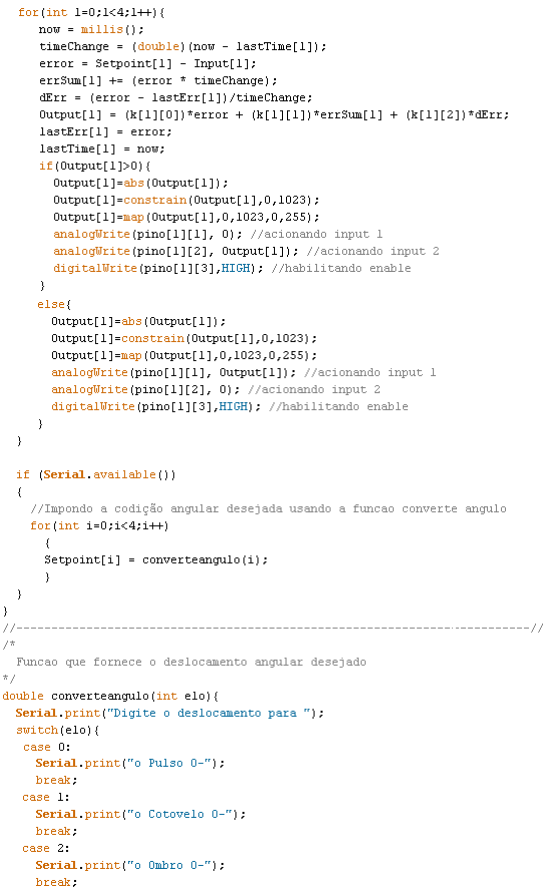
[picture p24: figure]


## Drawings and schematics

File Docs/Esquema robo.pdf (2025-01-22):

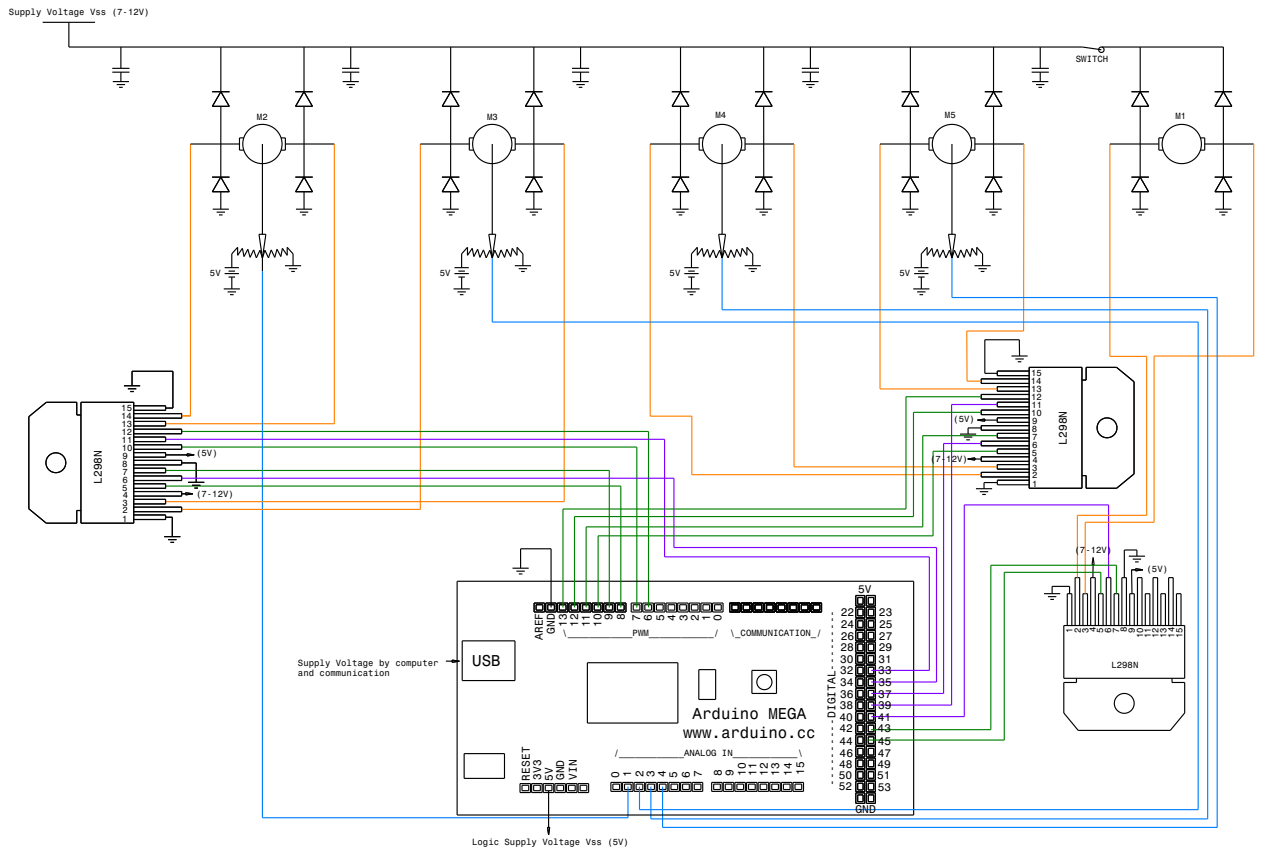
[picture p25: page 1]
/____________ANALOG IN____________\

Supply Voltage Vss (7-12V)

Supply Voltage by computer
and communication

Arduino MEGA
www.arduino.cc

Logic Supply Voltage Vss (5V)

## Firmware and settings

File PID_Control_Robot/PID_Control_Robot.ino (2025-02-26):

/*
Projeto de Sistemas Mecatrônicos
Alunos: Jorge Palma
        Vinicius Santos
        Valmir
*/

#include <PID_v1.h>

#define DRIVER_1_IN_1  10      // Motor 1 
#define DRIVER_1_IN_2  11      // Motor 1

#define DRIVER_1_IN_3  2      // Motor 2
#define DRIVER_1_IN_4  3      // Motor 2
#define DRIVER_2_IN_1  4      // Motor 3
#define DRIVER_2_IN_2  5      // Motor 3
#define DRIVER_2_IN_3  6      // Motor 4
#define DRIVER_2_IN_4  7      // Motor 4
#define DRIVER_3_IN_1  8     // Motor 5
#define DRIVER_3_IN_2  9     // Motor 5
#define DRIVER_3_IN_3  44     // RESERVA
#define DRIVER_3_IN_4  46     // RESERVA

// Definições para os potenciômetros e o fim de curso
#define POT_1_MOT_2 A0
#define POT_2_MOT_3 A1
#define POT_3_MOT_4 A2
#define POT_4_MOT_5 A3
#define FIM_DE_CURSO 42

#define MOTOR_1_MAX 1023//837  // Definir se esse máximo indica subida, descida, direita, esquerda
#define MOTOR_1_MIN 0//125
#define MOTOR_2_MAX 900//905
#define MOTOR_2_MIN 100
#define MOTOR_3_MAX 956
#define MOTOR_3_MIN 124
#define MOTOR_4_MAX 649
#define MOTOR_4_MIN 370
#define MOTOR_5_MAX 922
#define MOTOR_5_MIN 94

double set_point_mot_1, set_point_mot_2, set_point_mot_3, set_point_mot_4, set_point_mot_5;
double input_garra, input_mot_2, input_mot_3, input_mot_4, input_mot_5;
double output_mot_1_open, output_mot_1_close, output_mot_2_up, output_mot_2_down, output_mot_3_up, output_mot_3_down, output_mot_4_up, output_mot_4_down, output_mot_5_left, output_mot_5_right;

// Criando objetos PID e linkando as variáveis
//double kp_mot_1 = 0, kp_mot_2 = 1.1, kp_mot_3 = 1.4, kp_mot_4 = 2.0, kp_mot_5 = 1.2;
//double ki_mot_1 = 0, ki_mot_2 = 0.3, ki_mot_3 = 0.11, ki_mot_4 = 0.2, ki_mot_5 = 1;
//double kd_mot_1 = 0, kd_mot_2 = 0.9, kd_mot_3 = 1.7, kd_mot_4 = 1.1, kd_mot_5 = 0.0;

double kp_mot_1 = 0, kp_mot_2 = 1.1, kp_mot_3 = 0.5, kp_mot_4 = 2.0, kp_mot_5 = 1.2;
double ki_mot_1 = 0, ki_mot_2 = 0.0, ki_mot_3 = 0.3, ki_mot_4 = 0.0, ki_mot_5 = 0.0;
double kd_mot_1 = 0, kd_mot_2 = 0.0, kd_mot_3 = 0.0, kd_mot_4 = 0.0, kd_mot_5 = 0.0;


PID PID_Mot_1_open(&input_garra, &output_mot_1_open, &set_point_mot_1, kp_mot_1, ki_mot_1, kd_mot_1, DIRECT);
PID PID_Mot_1_close(&input_garra, &output_mot_1_close, &set_point_mot_1, kp_mot_1, ki_mot_1, kd_mot_1, REVERSE);

PID PID_Mot_2_up(&input_mot_2, &output_mot_2_up, &set_point_mot_2, kp_mot_2, ki_mot_2, kd_mot_2, DIRECT);
PID PID_Mot_2_down(&input_mot_2, &output_mot_2_down, &set_point_mot_2, kp_mot_2, ki_mot_2, kd_mot_2, REVERSE);

PID PID_Mot_3_up(&input_mot_3, &output_mot_3_up, &set_point_mot_3, kp_mot_3, ki_mot_3, kd_mot_3, DIRECT);
PID PID_Mot_3_down(&input_mot_3, &output_mot_3_down, &set_point_mot_3, kp_mot_3, ki_mot_3, kd_mot_3, REVERSE);

PID PID_Mot_4_up(&input_mot_4, &output_mot_4_up, &set_point_mot_4, kp_mot_4, ki_mot_4, kd_mot_4, DIRECT);
PID PID_Mot_4_down(&input_mot_4, &output_mot_4_down, &set_point_mot_4, kp_mot_4, ki_mot_4, kd_mot_4, REVERSE);

PID PID_Mot_5_left(&input_mot_5, &output_mot_5_left, &set_point_mot_5, kp_mot_5, ki_mot_5, kd_mot_5, DIRECT);
PID PID_Mot_5_right(&input_mot_5, &output_mot_5_right, &set_point_mot_5, kp_mot_5, ki_mot_5, kd_mot_5, REVERSE);

void setup()
{
  Serial.begin(9600);
  pinMode(DRIVER_1_IN_1, OUTPUT);
  pinMode(DRIVER_1_IN_2, OUTPUT);
  pinMode(DRIVER_1_IN_3, OUTPUT);
  pinMode(DRIVER_1_IN_4, OUTPUT);
  pinMode(DRIVER_2_IN_1, OUTPUT);
  pinMode(DRIVER_2_IN_2, OUTPUT);
  pinMode(DRIVER_2_IN_3, OUTPUT);
  pinMode(DRIVER_2_IN_4, OUTPUT);
  pinMode(DRIVER_3_IN_1, OUTPUT);
  pinMode(DRIVER_3_IN_2, OUTPUT);
  pinMode(DRIVER_3_IN_3, OUTPUT);
  pinMode(DRIVER_3_IN_4, OUTPUT);
  

  // Configuração dos PIDs
  PID_Mot_1_open.SetMode(AUTOMATIC);
  PID_Mot_1_close.SetMode(AUTOMATIC);
  PID_Mot_2_up.SetMode(AUTOMATIC);
  PID_Mot_2_down.SetMode(AUTOMATIC);
  PID_Mot_3_up.SetMode(AUTOMATIC);
  PID_Mot_3_down.SetMode(AUTOMATIC);
  PID_Mot_4_up.SetMode(AUTOMATIC);
  PID_Mot_4_down.SetMode(AUTOMATIC);
  PID_Mot_5_left.SetMode(AUTOMATIC);
  PID_Mot_5_right.SetMode(AUTOMATIC);

  PID_Mot_1_open.SetOutputLimits(0, 255);
  PID_Mot_1_close.SetOutputLimits(0, 255);
  PID_Mot_2_up.SetOutputLimits(0, 255);
  PID_Mot_2_down.SetOutputLimits(0, 255);
  PID_Mot_3_up.SetOutputLimits(0, 255);
  PID_Mot_3_down.SetOutputLimits(0, 255);
  PID_Mot_4_up.SetOutputLimits(0, 255);
  PID_Mot_4_down.SetOutputLimits(0, 255);
  PID_Mot_5_left.SetOutputLimits(0, 255);
  PID_Mot_5_right.SetOutputLimits(0, 255);

  // Definir o setpoint inicial
  set_point_mot_1 = 512; // Defina o valor desejado
  set_point_mot_2 = 512; // Defina o valor desejado
  set_point_mot_3 = 512; // Defina o valor desejado
  set_point_mot_4 = 520; // Defina o valor desejado
  set_point_mot_5 = 512; // Defina o valor desejado
}

void loop()
{
  if (Serial.available() > 0) {
    String input = Serial.readStringUntil('\n'); // Lê a string até o delimitador \0
    input.trim(); // Remove espaços extras

    // Divida a string com base na vírgula e atribua aos setpoints
    int motorValues[5];
    int index = 0;
    int pos = 0;
    while ((pos = input.indexOf(',')) != -1) {
      motorValues[index++] = input.substring(0, pos).toInt();
      input.remove(0, pos + 1);
    }
    motorValues[index] = input.toInt(); // Pega o último valor

    // Atribui os setpoints para cada motor de acordo com a ordem solicitada
    set_point_mot_5 = motorValues[4];
    set_point_mot_4 = motorValues[3];
    set_point_mot_3 = motorValues[2];
    set_point_mot_2 = motorValues[1];
    set_point_mot_1 = motorValues[0];

    Serial.print("Info received ");
    Serial.print(set_point_mot_5);
    Serial.print(" ");
    Serial.print(set_point_mot_4);
    Serial.print(" ");
    Serial.print(set_point_mot_3);
    Serial.print(" ");
    Serial.print(set_point_mot_2);
    Serial.print(" ");
    Serial.println(set_point_mot_1);
  }

  input_mot_2 = analogRead(POT_1_MOT_2);
  PID_Mot_2_up.Compute();
  PID_Mot_2_down.Compute();

  input_mot_3 = analogRead(POT_2_MOT_3);
  PID_Mot_3_up.Compute();
  PID_Mot_3_down.Compute();

  input_mot_4 = analogRead(POT_3_MOT_4);
  PID_Mot_4_up.Compute();
  PID_Mot_4_down.Compute();

  input_mot_5 = analogRead(POT_4_MOT_5);
  PID_Mot_5_left.Compute();
  PID_Mot_5_right.Compute();

  if (input_mot_2 > MOTOR_2_MIN && input_mot_2 < MOTOR_2_MAX)
  {
    if (input_mot_2 < set_point_mot_2)
    {
    //  Serial.print("if2-in: ");
    //  Serial.print(input_mot_2);
    //  Serial.print(" || out: ");
    //  Serial.print(output_mot_2_up);
      analogWrite(DRIVER_1_IN_4, output_mot_2_up);
      analogWrite(DRIVER_1_IN_3, 0);
    }
    else if (input_mot_2 > set_point_mot_2)
    {
    //  Serial.print(" else2-in: ");
    //  Serial.print(input_mot_2);
    //  Serial.print(" || out: ");
    //  Serial.print(output_mot_2_down);
      analogWrite(DRIVER_1_IN_4, 0);
      analogWrite(DRIVER_1_IN_3, output_mot_2_down);
    }
  }
  else
  {
    digitalWrite(DRIVER_1_IN_4, LOW);
    digitalWrite(DRIVER_1_IN_3, LOW);
  }


  if (input_mot_3 > MOTOR_3_MIN && input_mot_3 < MOTOR_3_MAX)
  {
    if (input_mot_3 < set_point_mot_3)
    {
    //  Serial.print(" if3-in: ");
    //  Serial.print(input_mot_3);
    //  Serial.print(" || out: ");
    //  Serial.print(output_mot_3_up);
      analogWrite(DRIVER_2_IN_2, output_mot_3_up);
      analogWrite(DRIVER_2_IN_1, 0);
    }
    else if (input_mot_3 > set_point_mot_3)
    {
    //  Serial.print(" else3-in: ");
    //  Serial.print(input_mot_3);
    //  Serial.print(" || out: ");
    //  Serial.print(output_mot_3_down);
      analogWrite(DRIVER_2_IN_2, 0);
      analogWrite(DRIVER_2_IN_1, output_mot_3_down);
    }
  }
  else
  {
    digitalWrite(DRIVER_2_IN_1, LOW);
    digitalWrite(DRIVER_2_IN_2, LOW);
  }


  if (input_mot_4 > MOTOR_4_MIN && input_mot_4 < MOTOR_4_MAX)
  {
    if (input_mot_4 < set_point_mot_4)
    {
    //  Serial.print(" if4-in: ");
    //  Serial.print(input_mot_4);
    //  Serial.print(" || out: ");
    //  Serial.print(output_mot_4_up);
      analogWrite(DRIVER_2_IN_4, output_mot_4_up);
      analogWrite(DRIVER_2_IN_3, 0);
    }
    else if (input_mot_4 > set_point_mot_4)
    {
    //  Serial.print(" else4-in: ");
    //  Serial.print(input_mot_4);
    //  Serial.print(" || out: ");
    //  Serial.print(output_mot_4_down);
      analogWrite(DRIVER_2_IN_4, 0);
      analogWrite(DRIVER_2_IN_3, output_mot_4_down);
    }
  }
  else
  {
    digitalWrite(DRIVER_2_IN_3, LOW);
    digitalWrite(DRIVER_2_IN_4, LOW);
  }

  if (input_mot_5 > MOTOR_5_MIN && input_mot_5 < MOTOR_5_MAX)
  {
    if (input_mot_5 < set_point_mot_5)
    {
    //  Serial.print(" if5-in: ");
    //  Serial.print(input_mot_5);
    //  Serial.print(" || out: ");
    //  Serial.println(output_mot_5_left);
      analogWrite(DRIVER_3_IN_2, output_mot_5_left);
      analogWrite(DRIVER_3_IN_1, 0);
    }
    else if (input_mot_5 > set_point_mot_5)
    {
    //  Serial.print(" else5-in: ");
    //  Serial.print(input_mot_5);
    //  Serial.print(" || out: ");
    //  Serial.println(output_mot_5_right);
      analogWrite(DRIVER_3_IN_2, 0);
      analogWrite(DRIVER_3_IN_1, output_mot_5_right);
    }
  }
  else
  {
    digitalWrite(DRIVER_3_IN_2, LOW);
    digitalWrite(DRIVER_3_IN_1, LOW);
  }

  delay(10); // Para facilitar a leitura do serial
}

// 512,512,250,520,512\0
// 512,390,650,400,512\0
// 512,640,250,400,268\0

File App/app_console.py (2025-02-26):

import serial
import time

# Definição dos limites de ângulo para cada motor
ANGLE_LIMITS = {
    1: (0, 360),  # Motor 1 é livre
    2: (36, 316),  # Motor 2 tem limites de 36° a 316°
    3: (44, 336),  # Motor 3 tem limites de 44° a 336°
    4: (131, 228),  # Motor 4 tem limites de 131° a 228°
    5: (34, 323),  # Motor 5 tem limites de 34° a 323°
}


def angle_to_value(angle):
    """Converte um ângulo (0° a 360°) para um valor entre 0 e 1023."""
    return int((angle / 360) * 1023)


def get_motor_setpoints():
    """Solicita ao usuário os ângulos para os 5 motores e verifica se estão na faixa permitida."""
    setpoints = []
    for i in range(1, 6):
        min_angle, max_angle = ANGLE_LIMITS[i]  # Obtém os limites do motor
        while True:
            try:
                angle = float(
                    input(
                        f"Enter the setpoint angle for motor {i} ({min_angle}° to {max_angle}°): "
                    )
                )
                if min_angle <= angle <= max_angle:
                    value = angle_to_value(angle)  # Converte para o intervalo 0-1023
                    setpoints.append(value)
                    break
                else:
                    print(
                        f"Invalid angle! Motor {i} accepts angles between {min_angle}° and {max_angle}°. Try again."
                    )
            except ValueError:
                print("Invalid input! Please enter a valid number.")
    return setpoints


def conectar_arduino(port, baudrate, tentativas=5):
    """Tenta conectar ao Arduino e retorna a instância Serial"""
    for _ in range(tentativas):
        try:
            ser = serial.Serial(port, baudrate, timeout=2)
            time.sleep(2)  # Aguarda inicialização do Arduino
            print("Conectado ao Arduino!")
            return ser
        except serial.SerialException:
            print("Tentando reconectar...")
            time.sleep(2)
    print("Falha ao conectar ao Arduino.")
    return None


def send_to_arduino(ser, setpoints):
    """Envia os setpoints para o Arduino via porta serial e aguarda resposta."""
    if ser is None or not ser.is_open:
        print("Erro: Porta serial não está aberta.")
        return False

    try:
        message = ",".join(map(str, setpoints)) + "\n"
        print(f"Sending: {repr(message)}")
        ser.write(message.encode())
        time.sleep(0.1)

        # Aguarda resposta do Arduino
        response = ser.readline().decode().strip()
        if response:
            print(f"Arduino response: {response}")
            return True
        else:
            print(
                "No response from Arduino. Check the connection and the Arduino code."
            )
            return False
    except serial.SerialException as e:
        print(f"Erro na comunicação serial: {e}")
        return False


def main():
    print("Welcome to the setpoints sending program for Arduino Mega!")
    port = input("Enter the COM port for communication (e.g., COM8): ")
    baudrate = 9600  # Taxa de transmissão padrão
    ser = conectar_arduino(port, baudrate)

    while True:
        setpoints = get_motor_setpoints()
        confirm = input(
            f"The setpoints are {setpoints} (converted values). Do you want to send them? (y/n): "
        ).lower()
        if confirm == "y":
            sucesso = send_to_arduino(ser, setpoints)
            if not sucesso:
                print("Tentando reconectar ao Arduino...")
                ser = conectar_arduino(port, baudrate)  # Tenta reconectar
        else:
            print("Restarting setpoints entry.")

        repeat = input("Do you want to send new setpoints? (y/n): ").lower()
        if repeat != "y":
            print("Exiting the program.")
            if ser and ser.is_open:
                ser.close()
            break


if __name__ == "__main__":
    main()

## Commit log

2024-12-19 Troca de variaveis e PID
2025-01-22 Inserindo arquivos de documentação e script. Arrumando também o diretório
    [Esquematico 1 motor.fzz]
2025-02-01 Update PID_Control_Robot.ino
    Adicionando outros controles dos motores
2025-02-04 Adicionando arquivos de scripts gerados na aula do dia 04/02
